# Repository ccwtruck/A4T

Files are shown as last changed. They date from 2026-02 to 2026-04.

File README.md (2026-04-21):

[][cc-by-nc-sa]

# A4T: [A]nother [4]010 [T]oolhead
A Toolhead from: ko-fi (https://ko-fi.com/O5O5OCC0K) [DW-Tas](https://github.com/DW-Tas)

Join me on Discord (https://discord.gg/NHbrD2AgW6)



<br/> 
After the last year or two looking after Xol and transforming it into Xol Toolhead, I thought it was about time I tried to see if I could design something from scratch. The result is A4T: [A]nother [4]010 [T]oolhead <br/><br/>

A4T is built around the following constraints:
* Dual 4010 blower fans for part cooling
* HF and some UHF hotends (originally designed around Dragon HF with an extender).
* 2510 hotend cooling with well-directed hotend cooling airflow. (Can't beat the amazing 5v Delta 2510)
* ***Easy Assembly***
* Custom Wrist Watch BMG mod with Sherpa-Mini spacing. Also works with Sherpa-Mini. (Some WWG2 and oribter options now too)
* Neopixel LEDs with good part lighting from in front of the nozzle.
* Built for Xol-Carriage - can work with Voron Tap / Standard Voron CW2 carriage.

> [!TIP] 
> ### NEW: Crossbow Filament Cutter And EMU MMU<br/>
> Make A4T part of a complete MMU system with the [Crossbow Filament Cutter](https://github.com/DW-Tas/Crossbow-Filament-Cutter) and [EMU](https://github.com/DW-Tas/EMU)<br/>
> 

## Pre-requisites
A printer that fits either Xol carriage, or a standard voron CW2 or Tap carriage. `NOT cartographer CNC carriage (see warning below)`<br/>
<br/>
To avoid build plate area loss:
- X/Y gantry joints that are within the same size as standard Voron 2.4 or Trident X/Y joints.
- Slimmer than stock idlers (see warning below) 

See Voron Design instructions to install TAP.<br/>
`If using tap, highly recommended to replace M3x50 SHCS with button head screws for better build plate clearance.`<br/>

> [!NOTE] 
> ### Notes for Xol-Carriage<br/>
> * Xol-Carriage documentation is here: https://github.com/Armchair-Heavy-Industries/Xol-Toolhead/blob/main/docs/xol_carriage_assembly.md<br/>
> * A4T uses standard length probe modules for Xol-Carriage (even with UHF hotends in A4T).<br/>
> * Monolith Gantry users should go with the Monolith specific Xol-Carriage mod: [Monolith_Xol-Carriage](https://github.com/Armchair-Heavy-Industries/Armchair-Usermods/tree/main/files/Xol-Toolhead/Monolith_Xol-Carriage)<br/>

<br/><br/>

> [!WARNING]
> ### Front Idlers  
> A4T can collide with the stock voron front idlers for Trident and 2.4 when the toolhead is in the front corners of the build area. This can cause issues with the homing sequence when homing X if the toolhead is at the front of the gantry on Y. <br/><br/>
> Fully compatible idlers:<br/>
> * clee's [BFI (Beefy Front Idlers)](https://github.com/clee/VoronBFI)  <br/>
> * Ramalama2's [Front Idlers](https://github.com/Ramalama2/Voron-2-Mods/tree/main/Front_Idlers)  

<br/><br/>

> [!WARNING]
> ### Cartographer CNC carriage  
>  The Cartographer CNC carriage is made for StealthBurner, not A4T. The probe will sit too low if used with A4T unless you have the tools and skill necessary to remove ~1.8mm off the bottom of the Cartographer CNC carriage mounting points where the probe attaches.

<br/>

## Bill of Materials (BOM)
***`*Not including carriage hardware`***
| Qty | Item | Notes |
| --- | --- | --- |
| 4 | M3 Square Nut (DIN 562) | Yes, square nuts. They don't spin in a slot like hex nuts |
| 3 | M3 x 8 SHCS | 2x Top cowling mounting. 1x Toolhead board mount to back of Xol Carriage |
| 2 | M3 x 6 BHCS or Waferhead screw | Either of these screw types work. The important part is 6mm thread <br/> `This is only for Xol Carriage. If you use Tap or other Voron carriage, you already have longer SHCS where the hotend adapter slots under` tap screws | 
| 2 | M3 x 50 SHCS | Bottom cowling mounting screws. The same as are in the bottom of Stealthburner |
| 2 | * M3 x 16 SHCS or BHCS (WWBMG)<br/><br/>* M3 x 12 SHCS or BHCS (Sherpa-Mini)<br/><br/>* 1xM3 x 20 + 1xM3 x 16 SHCS or BHCS (WWG2) | Attach extruder to cowling |
| 2 | 4010 Blower Fan | Recommended blower: GDStime 12,000 RPM 24v. (<a href="https://www.aliexpress.com/item/1005005094153190.html">Ali Express</a>) <br/><br/>`⚠️ HoneyBadger 9K 4010 fans known to be incompatible (12K version is OK).`<br>~~`BERSERKER VINDR 4010`~~ `Newer BERSERKER 4010s have an updated design and should be OK` |
| 1 | 2510 Axial Fan | Recommended fan: Delta Electronics 15,000 RPM 5v ASB02505SHA-AY6B (<a href="https://www.digikey.com/en/products/detail/delta-electronics/ASB02505SHA-AY6B/7491489">DigiKey</a>) <br/><br/> `⚠️ GDStime 2510 fans have been measuring as ~10.4mm thick. A workaround is to "sink" the hotend fand duct 0.4mm into the print bed with the slicer before printing.`|
| 3 | Neopixel LED PCB | The same kind as used in Stealthburner. Get the solder pad version. <br/> `Wiring diagram (click to enlarge) ---->`  LEDs  <br/>`Different length wires for different Cowling types` |
| 9 | Lengths of 28 AWG or 26 AWG wire | To make the LED harness |
| 1 | Connector and required crimps | To make the LED harness |
| 1 | Hotend | Recommended hotend:<br/>*  **Dragon HF** with **Triangle Lab ZS-MZE-HF** (<a href="https://trianglelab.net/products/mze%E2%84%A2-dlc-v6-melt-zone-extruder">trianglelab.net</a>)Dragon <br/> Alternatives: <br/>* Chube Compact <br/>* Dragon UHF or UHF-Mini <br/>* Dragon Ace `use the included 3mm spacer`<br/>* Dragon Ace with MZE `use the included 3mm spacer`<br/>* Rapido HF or UHF<br/>* NF-Crazy Volcano `May melt plastic behind status LED without tape insulation` <br/>* Revo-Voron<br/>* Bambulab<br/>* TZ-V6-2.0 <br/><br/>`volcano blocks with oversize heater cartridges may require some insulation tape (aluminium/reflective) on the back of the LED housing that faces the hotend.` |
| 4 | Hotend screws | Should come with your hotend. Dragon/Rapido usually use M2.5 x 8mm SHCS |
| 1 | Extruder | Recommended Extruder:<br/>* Modified WW-BMG with Bondtech RIDGA v2. ([Details here](STL/WW-BMG%20for%20A4T/))<br/> Alternatives: <br/>*Sherpa-Mini  <br/>*VZ-Hextrudort-Low <br/>*LGX-Lite <br/>*E3D Roto Vitamins <br/>*Wrist-Watch G2 <br/>*Orbiter 2.0 <br/> <br/>`⚠️ Sherpa-Mini not supported with UHF hotends` |
| 2 | 20mm or 21mm 3mm internal threaded stand off  | To attach toolhead board to the back of the extruder motor and third mounting point on the back of Xol Carriage. <br/>`Length will depend on the motor you use. It needs to line up the toolhead board holder with the back of the Xol Carriage.` |
| 2 | M3 Threaded heatset inserts  | Standard Voron spec M3x4x5 `For the toolhead board mount` |

Additional BOM for the WW-BMG extruder for A4T can be found here: [STL/WW-BMG for A4T/README.md](<STL/WW-BMG for A4T/README.md>)

## Printing parts

> [!TIP] 
> ### Printed Parts Configurator<br/>
> <br>
> A great way to understand which files to print is by using the configurator at <a href="https://a4t.dwtas.net/">https://a4t.dwtas.net/</a><br><br>
> That configurator is new and not heavily tested, if you have issues, there is this original configurator by <a href="https://github.com/Corunir">Corunir</a>: <a href="https://a4t.wizards-enclave.net/">https://a4t.wizards-enclave.net/</a>

### Print settings
Parts are meant to be printed in 0.2mm layer heights, 0.25mm first layer should be OK. Other layer heights will cause the built-in supports to fail or fuse to the printed part.<br/>
Print settings will depend on your printer setup / filament used / phase of the moon/etc.<br/>
The parts are not pre-scaled for any particular filament type. You will need to tune the filament you use for correct shrinkage compensation to get good results. Development was done with multiple brands of ASA and ASA-CF filaments (each individually tuned).<br/>

General voron-like settings are a good starting point for 0.4mm wall widths (four walls, 5 top/bottom layers and 40% infill).<br/>
The print setup was tested with 0.5mm nozzle printing 0.55mm line widths with 3 walls and 40% infill with good results.<br/>

You're printing a toolhead, not a trinket or a toy. You should be aiming for high strength with strong layer adhesion. I.e. print it slower/hotter if you have bad layer adhesion. It doesn't matter if it takes over 2 hours to print the main body.
<br/><br/><br/><br/>

> [!WARNING]
> ### Blower fan fit  
> `If your blower fans are not a slight friction fit, you likely had shrinkage compensation or EM issues. You can probably get away with using some masking tape on top of a loose fan to save a reprint in a pinch.` <br/>
> <br/>
> Fans should go in with a slight friction fit. DO NOT FORCE THEM IN. Your print settings aren't right if the fans are too tight. More shrinkage compensation or less EM depending on if you're over extruding or not.

## Assembly
### LED Harness (optional)
(click to open full size image)<br/>
LED Harness<br/>
Skinny wire needed, read the BOM.

### Assembly Steps

| <center>Notes</center> | Images|
| --- | :-----: |
| Remove the built-in supports from the printed parts|<br/><br/> |
| Attach the LED filter to the LED diffuser. <br/>`a drop of superglue is handy here` |  |
| Install the LED filter/diffuser assembly into the cowl <br/>`it should push into place and stay put` |  |
| Put the Status LED into the LED carrier <br/>`the one closest to the connector` |  |
| Install the LED harness into the Cowl | |
| &nbsp; &nbsp; &nbsp;1. Thread the two nozzle LEDs through the holder part of the cowl from the top and out the bottom |  |
| &nbsp; &nbsp; &nbsp;2. Install the middle LED of the chain into it's slot <br/><br/> `If the LEDs are tight to insert, run a small flat head screwdriver along the edges of the LED slots to open them up a bit.` |  |
| &nbsp; &nbsp; &nbsp;3. Put the last LED into the other slot |  |
| &nbsp; &nbsp; &nbsp;4. The wires between the 2nd and 3rd LED go back up over the top of the Status LED holder |  |
| Put the 2510 HE fan in place. <br/>`It will need to be angled in, slightly top first. The wires should be exiting from the top` <br/><br/> `⚠️ Don't push on the hub of the fan 😢`  |  |
| Lock the 2510 HE fan in place by sliding the HE fan duct up until the flexture locks.<br/>`⚠️ Careful, don't pinch any wires`|  |
| Tidy up the LED harness wires in the little hooks. `the left blower fan will lock them in soon` |  |
| ***Install the 4010*** ~~inserts~~ ***backflow inhibitors*** | |
| &nbsp; &nbsp; &nbsp;1. take the front cover off the 4010 blower fan<br/>`This is easy on gdstime fans, but requires careful prying on Delta fans as they use some glue in manufacturing`  |  |
| &nbsp; &nbsp; &nbsp;2. Use some superglue or acetone to glue the ~~insert~~ ***backflow inhibitor*** in place<br/>`Use the spacer to line it up properly` |  |
| &nbsp; &nbsp; &nbsp;3. Put the front cover back on the fan |  |
| &nbsp; &nbsp; &nbsp;4. Remove the little handle and sand/file the ~~insert~~ ***backflow inhibitor*** flush with the blower opening |  |
| Time to put the blower fans in `Slide them into each side with the opening at the bottom`  <br/><br/>`*Fans should go in with a slight friction fit. DO NOT FORCE THEM IN. Your print settings aren't right if the fans are too tight. More shrinkage compensation or less EM depending on if you're over extruding or not.` |  |
| Attach your hotend |  |
| Put all the square nuts in their places for later |  |
| &nbsp; &nbsp; &nbsp;* Two under the extruder mounting points |  |
| &nbsp; &nbsp; &nbsp;* Two in the back behind the extruder `Xol-Carriage only` |  |
| ***Main cowl is ready, time for the extruder*** | |
|If you're building the WW-BMG for A4T see instructions here:|[STL/WW-BMG for A4T/README.md](<STL/WW-BMG for A4T/README.md>)|
| Make sure you used long enough screws to hold your stepper motor to the extruder and install the 20mm standoffs behind the motor |  |
| Attach the toolhead board mount and toolhead board to the standoffs `THB mounts, except for Sherpa-Mini, need 2x M3 heatsets installed before this step`<br/><br/>`⚠️ Use button head cap screws to attach the THB mount to the stand offs so that the THB pins don't touch the screws.` |    |
| Put the Extruder Adapter in place on top of the cowl<br/>`*Not used with Sherpa-Mini or on UHF hotend cowls` <br/><br/>`⚠️ Don't forget the PTFE tube between extruder and hotend` |  |
| :information_source: **Clockwork2 carriage/Tap users**: Don't forget the 2x M3x8 SHCS that go behind the adapter |  |
| Attach the extruder to the main cowl <br/><br/>`⚠️ If using G2/Orbiter cowl for CW2/Tap carriage, the right screw for the extruder has to wait until the end.`  |  |
| Time to wire it all up |  |
| &nbsp; &nbsp; &nbsp;Make sure to keep wires out of the carriage screw keep clear zone |  |
| &nbsp; &nbsp; &nbsp;Use the cable tie slots to keep everything tidy |  |
| ***Finally, we can put this thing on the printer!*** | |
| Ensure the screws already in the carriage have more than 3mm of exposed thread to hook the toolhead on to. <br/>`If they don't, the toolhead won't be able to slot into place` |  |
| Put the third toolhead board mounting screw into the back of Xol carriage, leaving 4 to 5mm of exposed threads |  |
| Hook the toolhead board mount over third mounting screw and slide the completed toolhead down onto the screws that are pre-placed in the carriage. |  |
| Tighten up all the screws:<br/>* 2x M3x50 bottom screws<br/>* 2x screws that were already in the carriage `access via the driver holes`<br/>* 2x M3x8 top screws<br/>&nbsp; &nbsp; &nbsp;** From the front for CW2/Tap<br/>&nbsp; &nbsp; &nbsp;** From the back for Xol Carriage<br/>* 1x M3x8 under the toolhead board (Xol Carriage only) |     |
| Remember to hook up your probe wires from the carriage to the toolhead board, if you're using one. <br/>`and your endstop wires if you haven't figured out sensorless yet` | |
| Make sure you double check your software setup `especially endstop location` | |

<br>

### The Results
After six months of development, CAD, CFD, trial and lots of error. Finally, A4T has better IS results, better cooling results and a new look compared to what I have been doing the last few years.

This is a comparison of part cooling between Xol and A4T. 
These prints were completed on the same printer, with the same gcode, same filament, the same hotend and part cooling fans (~~inserts~~ ***backflow inhibitors*** installed for A4T test).
Comparison

CFG

## Licenced kits
Licenced kits for A4T are available from the following manufucturers:<br/>

| Manufacturer | Purchase Link |
| --- | --- |
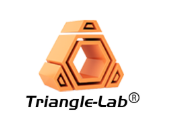
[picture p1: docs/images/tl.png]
|  | https://aliexpress.com/item/1005011869753607.html |
|  | https://aliexpress.com/item/1005011905019224.html |

### Credits
* The helpful Crew and Contributors at Voron Design
* Big shoutout to [yellowfish543](https://github.com/yellowfish543/StdToolheadOpenfoam/) for the CFD insights that unlocked the potential of this design.
* weaslus for insisting that the 4010 inserts get renamed to "backflow inhibitors"
* Corunir for the configurator wizard

> [!TIP] 
> ### You can help support the development of Armchair Projects.<br/>
> Donate at https://ko-fi.com/armchair<br/>
ko-fi (https://ko-fi.com/armchair)

## Enjoy using A4T
This work is licensed under a
[Creative Commons Attribution-NonCommercial-ShareAlike 4.0 International License][cc-by-nc-sa].

[][cc-by-nc-sa]

[cc-by-nc-sa]: http://creativecommons.org/licenses/by-nc-sa/4.0/
[cc-by-nc-sa-image]: https://licensebuttons.net/l/by-nc-sa/4.0/88x31.png
[cc-by-nc-sa-shield]: https://img.shields.io/badge/License-CC%20BY--NC--SA%204.0-lightgrey.svg

### License clarification regarding non-commercial use:
The non-commercial aspect of this license is for cases where A4T is the product, not the use of A4T to create products.<br/>
I.e. If you wish to sell A4T as a product, you would need to seek a commercial license before doing so. </br>
It is NOT intended to prevent the use of A4T in a printer that you use to provide commercial services. If you want to run A4T as a toolhead for your print farm printers, go right ahead.

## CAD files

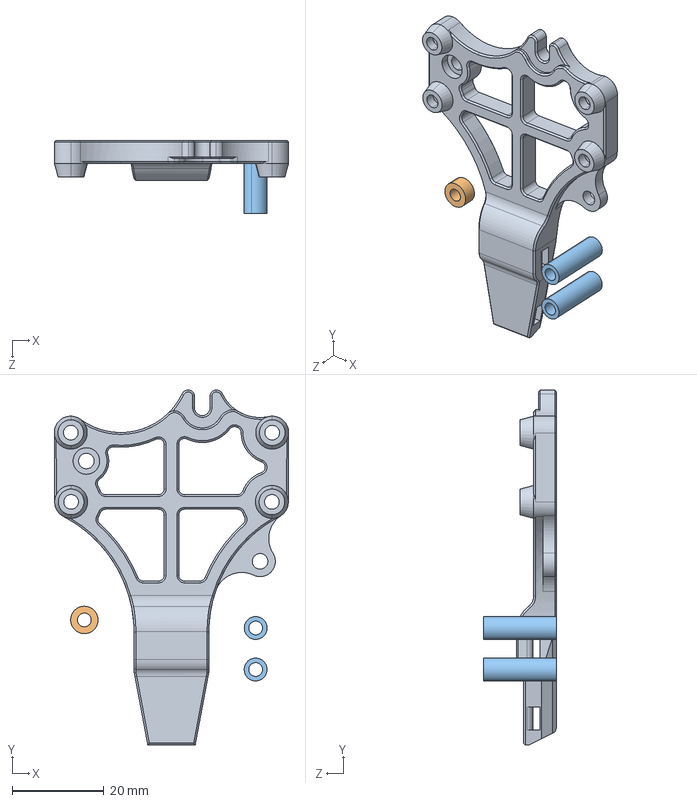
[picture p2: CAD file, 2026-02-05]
CAD/Toolhead Board Mounts/A4T - THB Mount - Orbiter - NH36.step
51.2 x 77.5 x 16.0 mm
A4T - THB Mount - Orbiter v2.0 - NH36
standoff3-26
standoff16 x 2

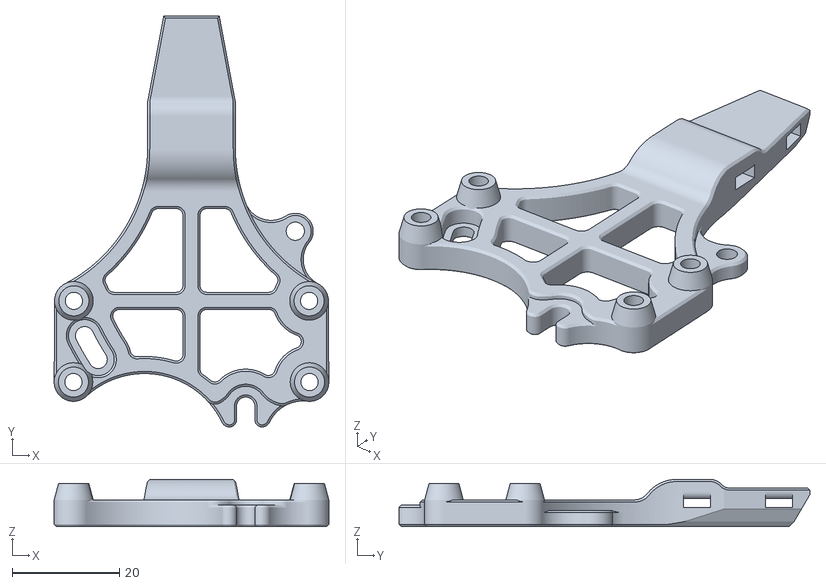
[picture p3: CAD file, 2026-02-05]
STL/Toolhead Board Mounts/A4T - THB Mount - WWBMG - NH36.STL
51.2 x 76.6 x 8.80

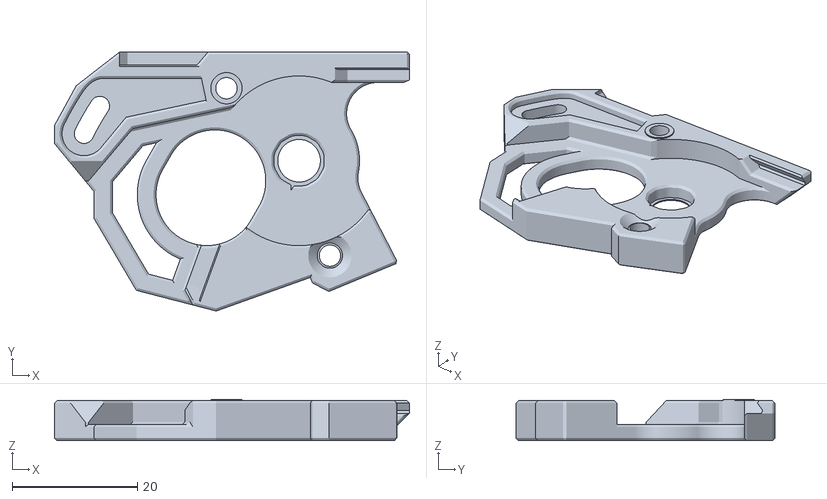
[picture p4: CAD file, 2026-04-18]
STL/WW-BMG for A4T/Dual Sensor/A4T - WWBMG - Motor_Plate - Dual Sensor.stl
56.7 x 41.4 x 6.60

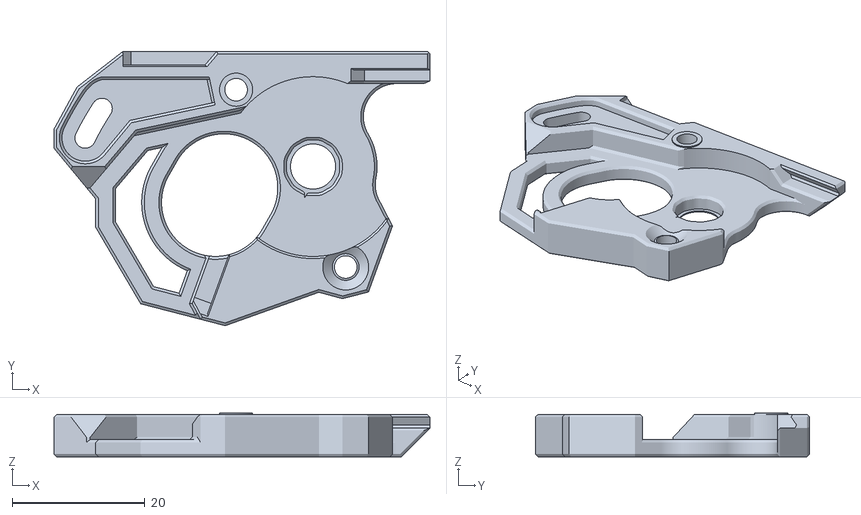
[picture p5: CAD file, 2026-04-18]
STL/WW-BMG for A4T/Standard (no sensor)/A4T - WWBMG - Motor Plate.stl
56.7 x 41.4 x 6.60

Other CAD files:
3mf/Toolhead Board Mounts/A4T - THB Mount - Orbiter - NH36.3mf
STL/Toolhead Board Mounts/A4T - THB Mount - Orbiter - NH36.stl

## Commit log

2026-02-05 Add NH36 mount for Orbiter extruder (#23)
    * Add NH36 mount for WW-BMG extruder.
    This update adds support for the Nitehawk-36 LDO toolboard and introduces a new toolhead board mount designed specifically for the WW-BMG extruder used in the A4T setup.
    * Orientation adjusted
    Orientation adjusted so that it fits neatly on the print bed.
    * Orientation adjusted
    Correct this time :-)
    * Add NH36 mount for Orbiter extruder
    This update adds support for the Nitehawk-36 LDO toolboard and introduces a new toolhead board mount designed specifically for the Orbiter extruder used in the A4T setup.
    [A4T - THB Mount - Orbiter - NH36.3mf, A4T - THB Mount - Orbiter - NH36.step, A4T - THB Mount - Orbiter - NH36.stl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]
2026-04-18 upload WW-BMG updated motor plate files
    [A4T - WWBMG - Motor Plate.stl, A4T - WWBMG - Motor_Plate - Dual Sensor.stl, A4T - WWBMG - Motor_Plate - Single Sensor.stl]

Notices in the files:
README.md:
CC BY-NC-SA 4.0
